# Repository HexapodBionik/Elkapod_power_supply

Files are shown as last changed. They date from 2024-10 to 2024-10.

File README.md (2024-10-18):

# Elkapod Power Supply
Elkapod Power Supply is a power supply for a hexapod walking robot built as part of the work in the Warsaw University of Technology Bionik science club. It provides power to 18 leg servos, electronics and peripherals.

---

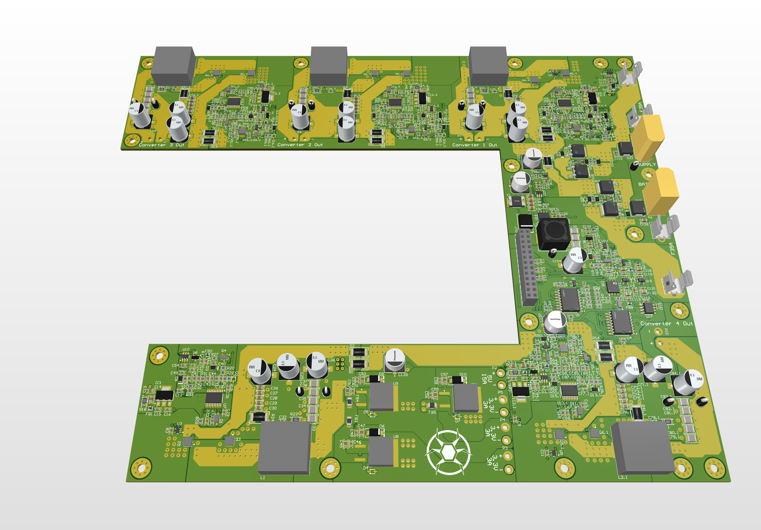
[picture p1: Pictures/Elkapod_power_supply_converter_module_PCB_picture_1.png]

The bottom PCB - Converter Module

---


The upper PCB -  Controller Module

## Design assumptions
The servos used in the project draw a maximum current of 3.5A according to the documentation. For this reason, the power supply should provide a current of around 60A. This power supply can be powered from an external mains power supply with a voltage of 11 to 18V, and from a lithium-ion battery with a similar voltage range. Therefore, it was decided to make 3 buck converters with a maximum current of 20A, which allow for tuning the output voltage in the range of 5.0-7.5V. Additionally, one 5V buck converter with a capacity of 15A was made to power the robot's electronics. The possibility of equipping the robot with an additional manipulator was also taken into account, by making an additional buck converter with a voltage regulated in the range of 5-9.5V and an output current of up to 20A. Additional requirements imposed on the power supply design were: measurement of the current of each servos, the ability to turn off the power supply of each servos separately, the use of logic level converters to control the servos using PWM from an external Elkapod Hardware Controller, additional controlled and uncontrolled 3.3V and 5V outputs, stand-by voltage outputs, voltage measurements, error status memory, communication with the battery pack using the SMBus protocol. All this is to be controlled from an external Elkapod Hardware Controller using the CAN bus.

The lower PCB contains 5 main converter sections, a stand-by converter and a power selector with reverse polarity protection implemented on MOSFET transistors.

The upper PCB contains circuits for measuring currents, controlling servos, a simple user interface based on buttons and LEDs and an STM32 microcontroller.

## Description of connectors

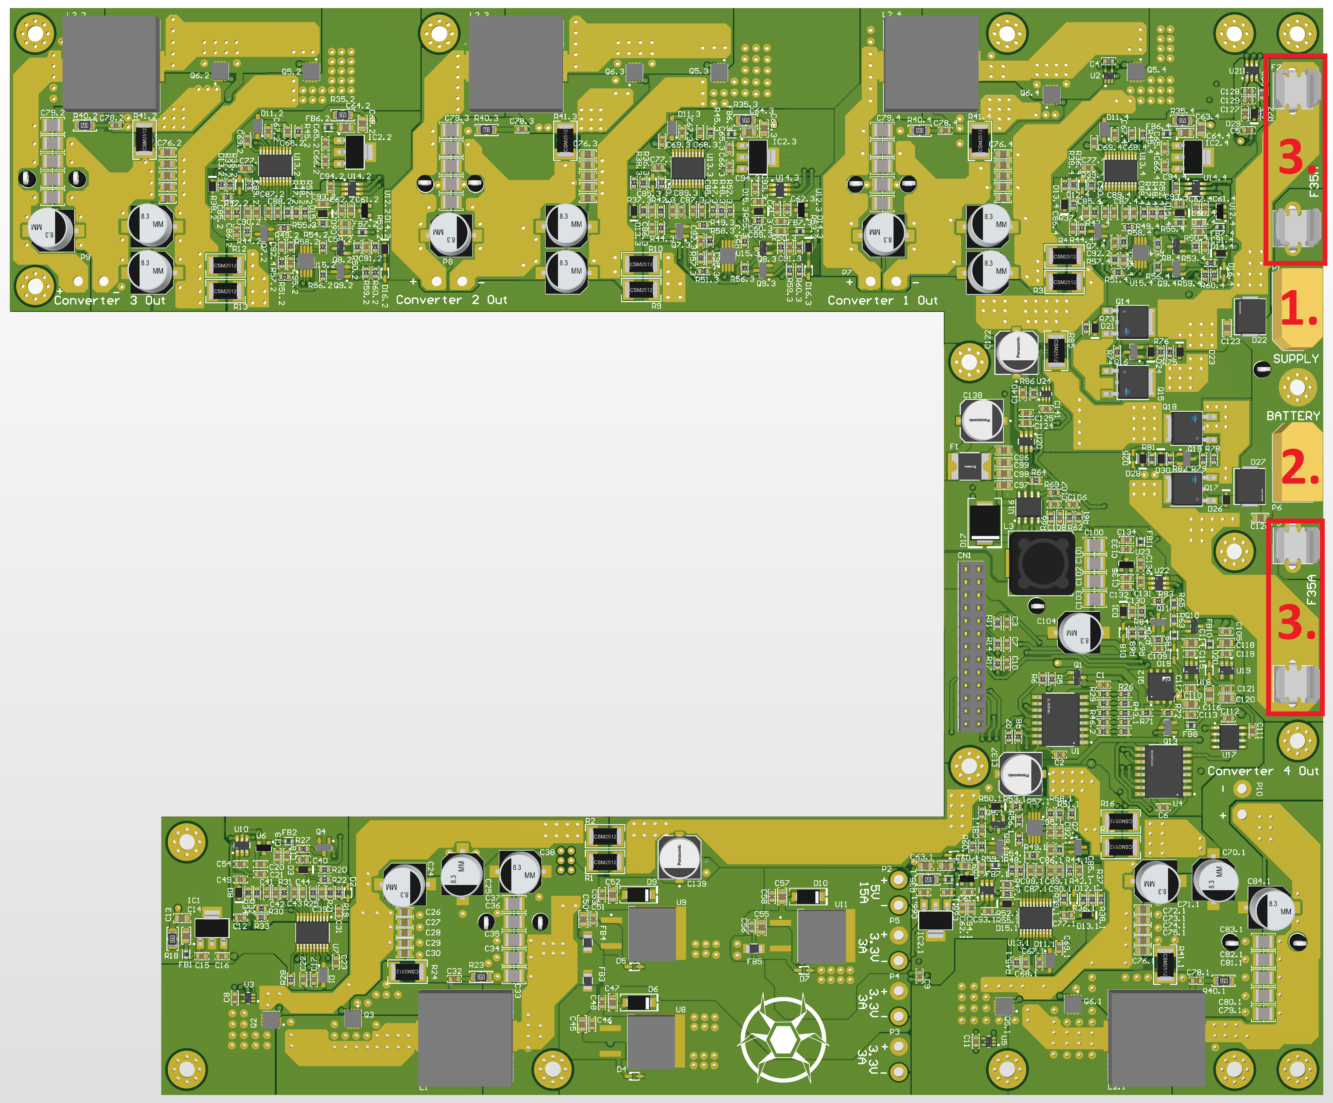
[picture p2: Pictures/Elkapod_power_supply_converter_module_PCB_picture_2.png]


The lower PCB:

1. External power supply XT60 connector (11-18V, min. 35A);
2. Li-ion battery pack XT60 connector (4s configuration);
3. 35A 6.3x32mm fast fuses connectors;

---

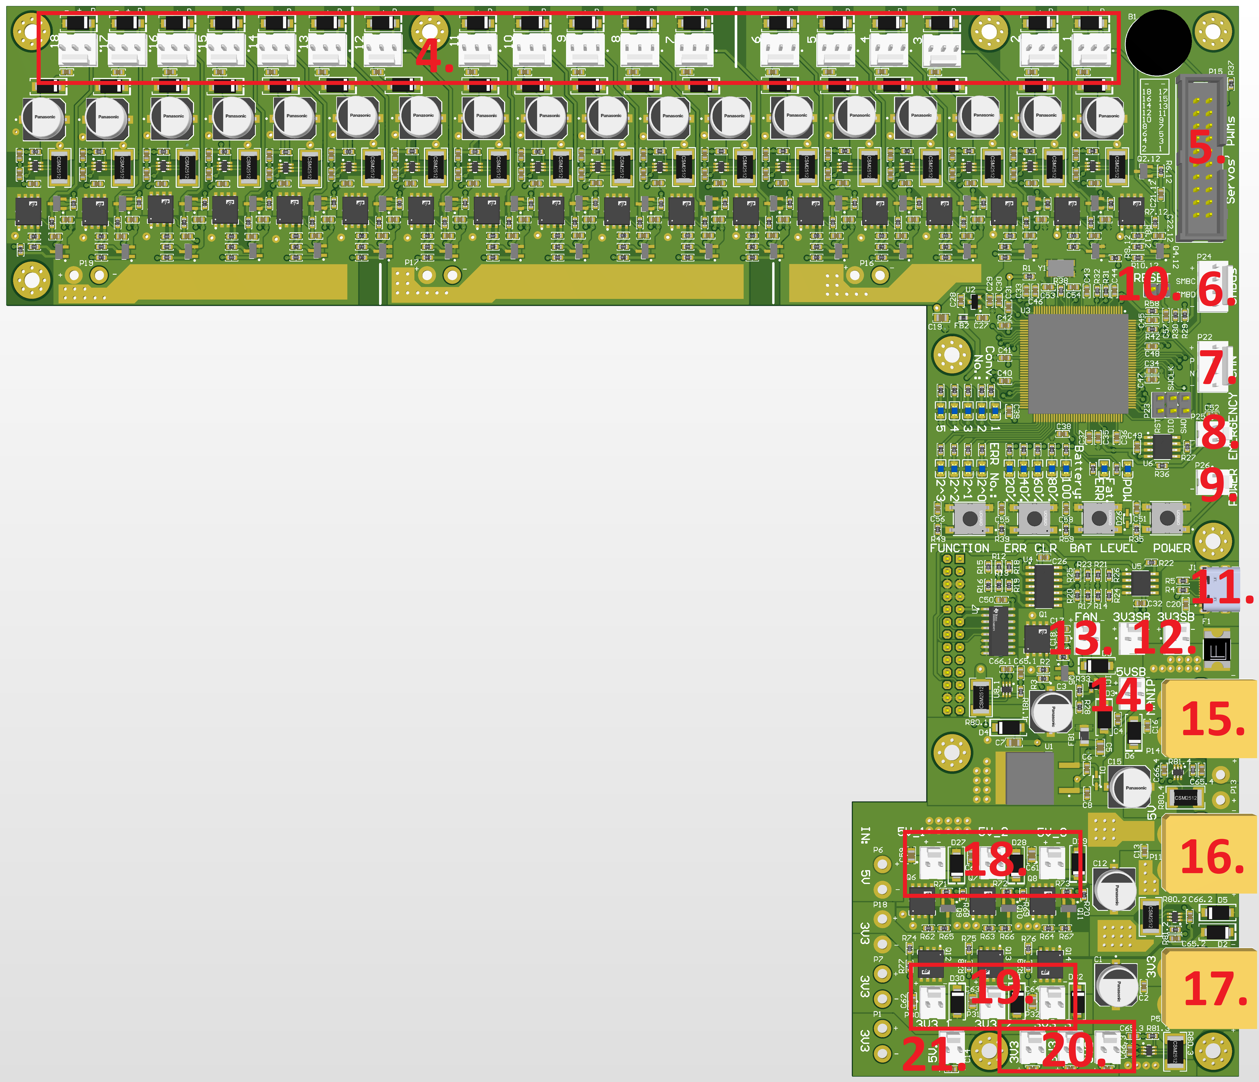
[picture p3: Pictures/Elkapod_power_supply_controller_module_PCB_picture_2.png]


The upper PCB:

4. 18 x servos connectors (5.0-7.5V; 3.5A);
5. IDC20 connector to control servos with PWM;
6. SMBus KK connector to control the battery li-ion pack;
7. CAN KK connector;
8. Emergency button KK connector (OFF-(ON) type);
9. Power button KK connector (OFF-(ON) type);
10. Reset goldpin jumper;
11. USB-C supply connector (5V; 5A);
12. 3.3V stand-by voltage KK connectors (sum of all 3.3V and 5V currents up to 2.5A);
13. Optional fan KK connector (5V; 100mA);
14. 5V stand-by voltage KK connector (sum of all 3.3V and 5V currents up to 2.5A);
15. Manipulator supply XT60 connector (5.0-9.5V; 20A);
16. 5V power out XT60 connector (up to 15A but sum of all 3.3V and 5V currents (except stand-by voltages) cannot exceed 15A);
17. 3.3V power out XT60 connector (3A);
18. 5V controllable (turn on and off via CAN bus) KK connectors (3 x 2.5A);
19. 3.3V controll controllable (turn on and off via CAN bus) KK connectors (3 x 2.5A but sum of all this currents cannot exceed 3A);
20. 3.3V KK connectors (3 x 2.5A but sum of all this currents cannot exceed 3A);
21. 5V KK connector;

## Safety information
The device is built exclusively from MOSFET transistors and integrated circuits in MOS technology, which makes it very sensitive to ESD (electrostatic discharge). All connectors are protected against ESD using Transil diodes, but this does not protect against damaging the board by touching it in other places. Therefore, it is forbidden to touch the power supply without appropriate anti-ESD protection.

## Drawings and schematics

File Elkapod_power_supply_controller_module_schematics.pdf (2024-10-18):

# DC Outputs

# Currents Measurement

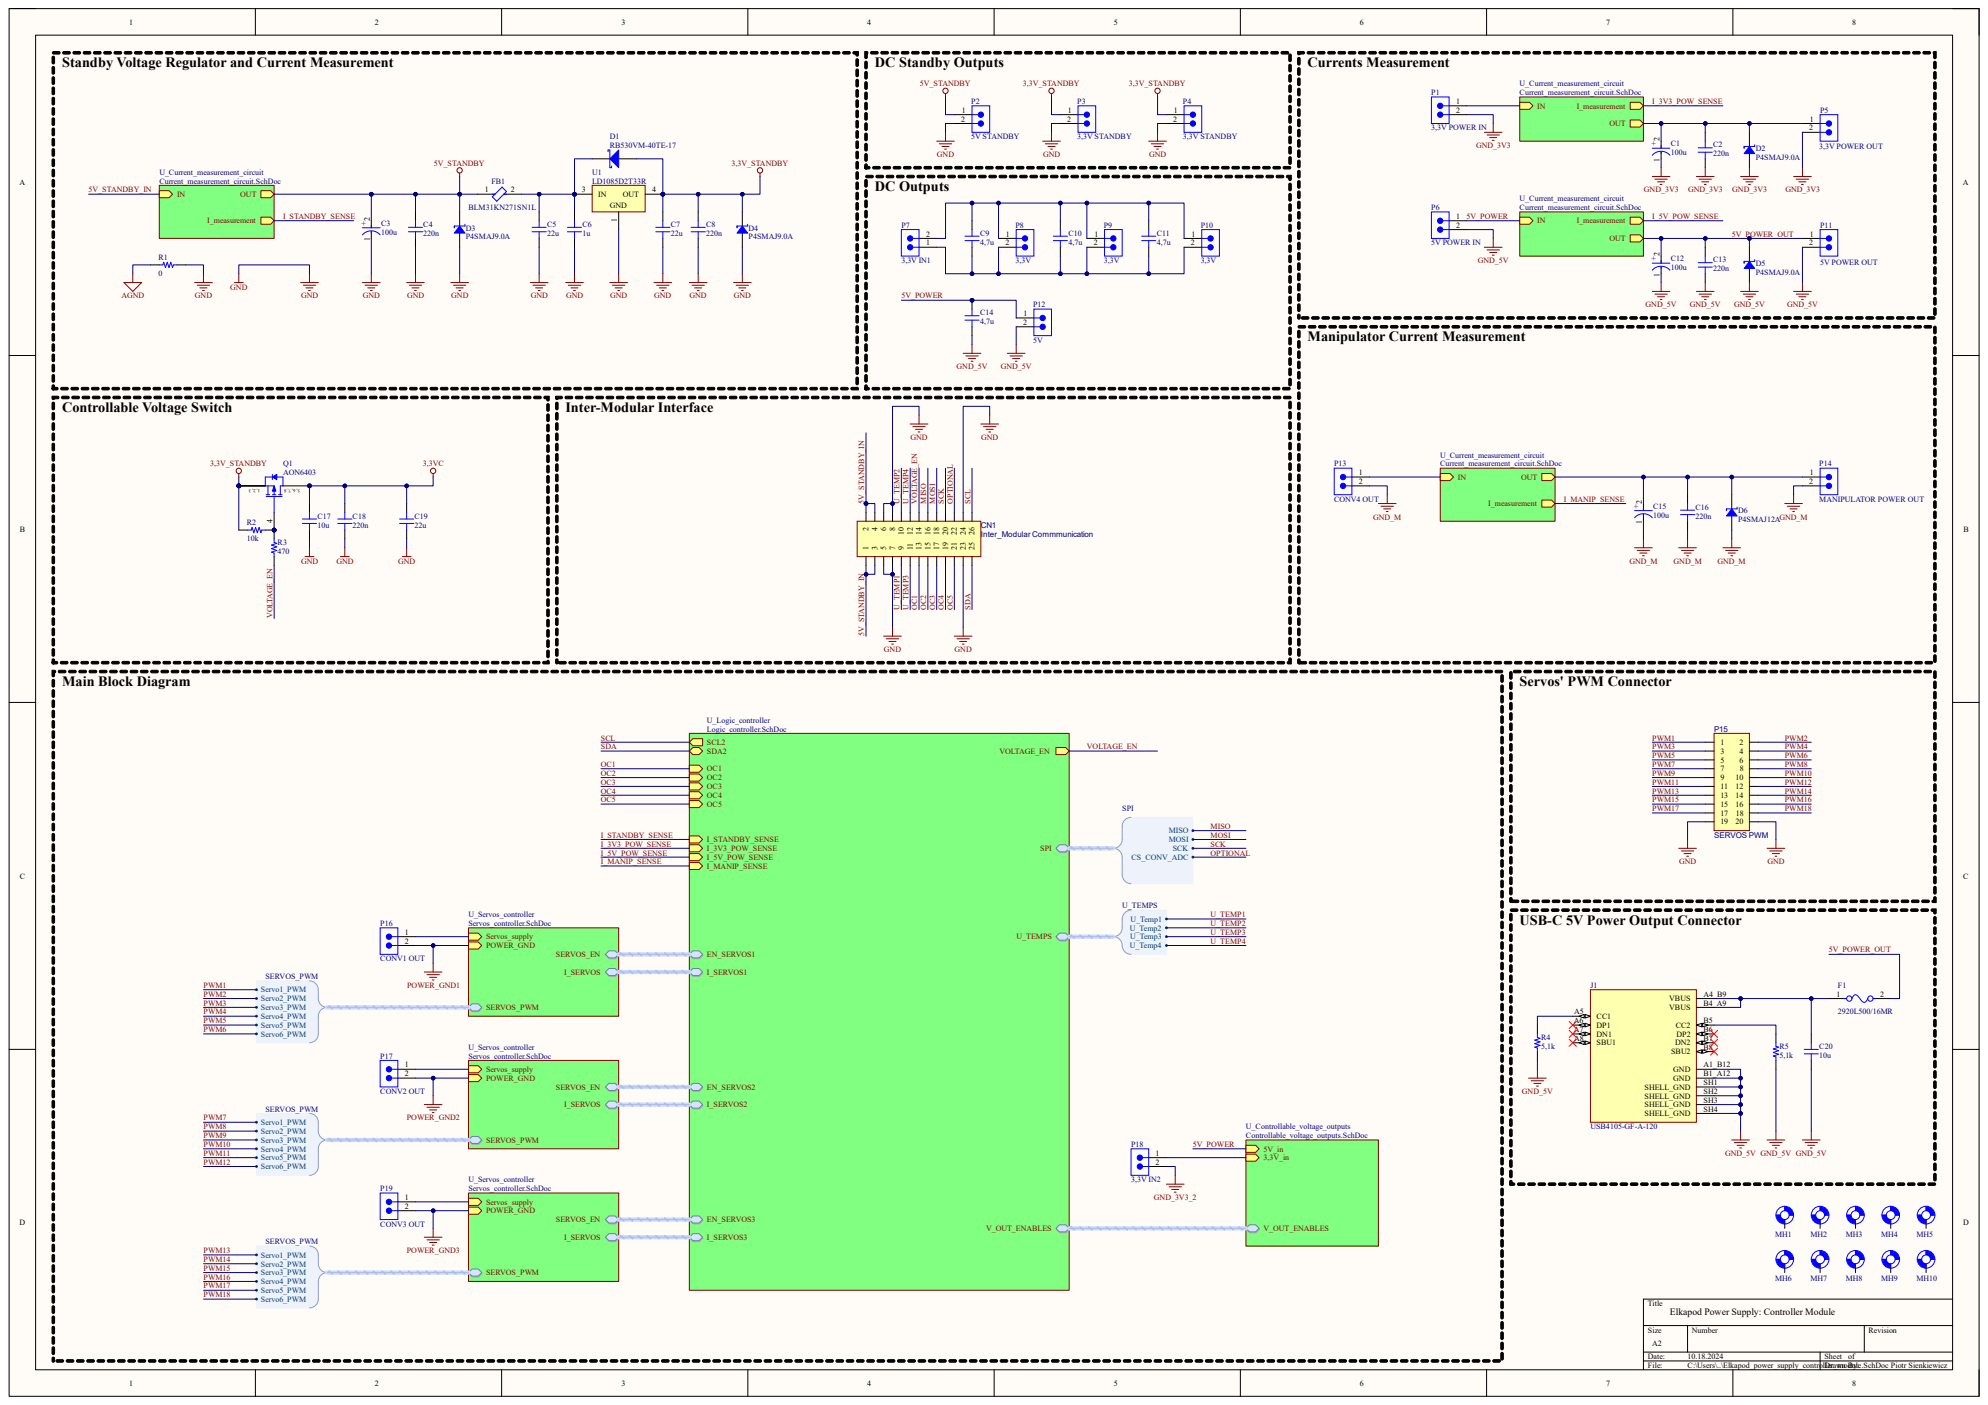
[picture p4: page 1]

Standby Voltage Regulator and Current Measurement

USB-C 5V Power Output Connector

Title
Elkapod Power Supply: Controller Module

A A

# Servos_supply

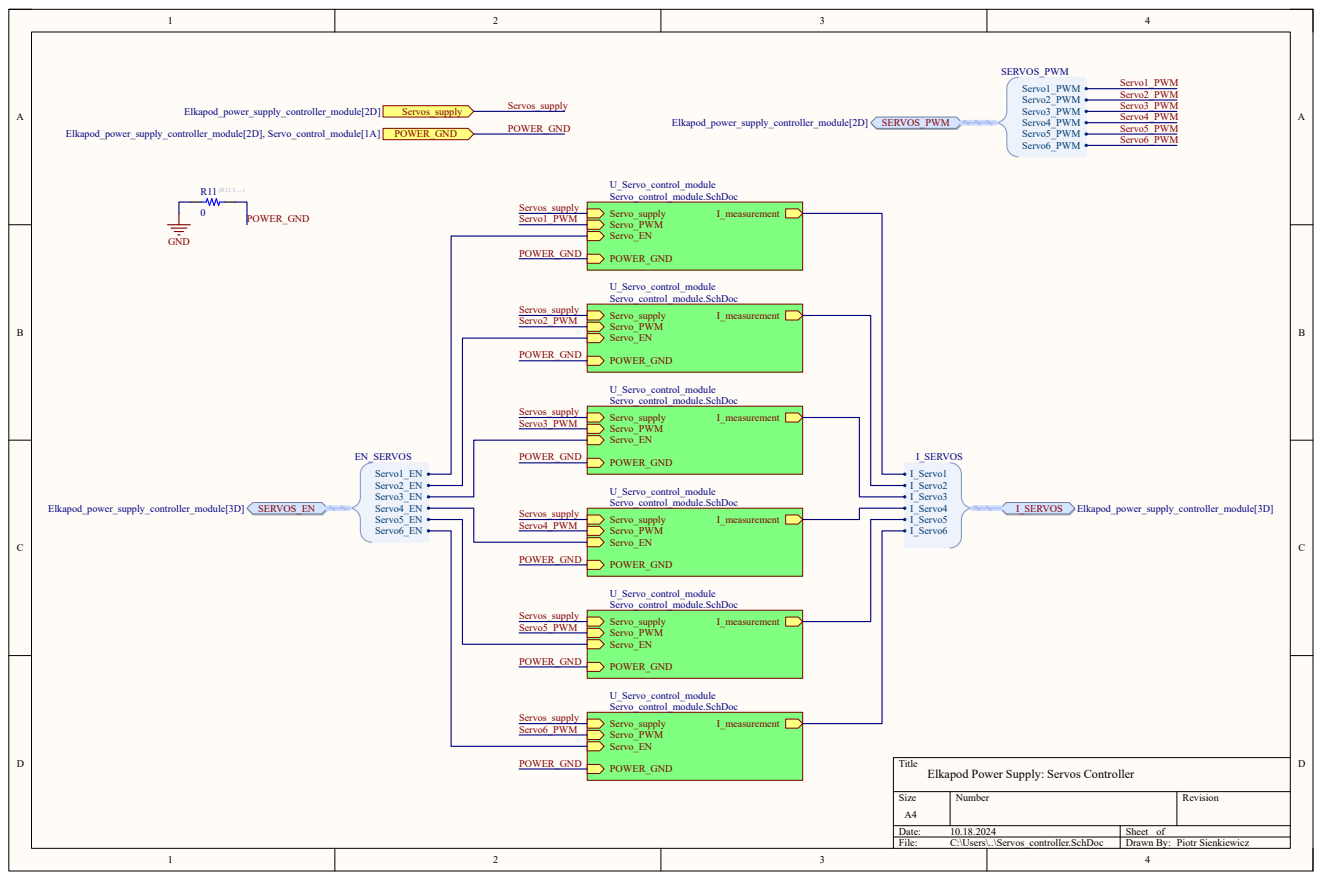
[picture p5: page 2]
Size; Number; Revision; File:; C:\Users\..\Servos_controller.SchDoc; Drawn By:; Servos_supply; Servo1_PWM; Servo2_PWM; Servo3_PWM; Servo4_PWM; Servo5_PWM; Servo6_PWM; Servo_supply Servo_PWM; I_measurement; Servo_EN; POWER_GND; U_Servo_control_module Servo_control_module.SchDoc; Elkapod_power_supply_controller_module[2D]; I_Servo1 I_Servo2 I_Servo3 I_Servo4 I_Servo5 I_Servo6; I_SERVOS; Elkapod_power_supply_controller_module[3D]; Servo1_EN Servo2_EN Servo3_EN Servo4_EN Servo5_EN Servo6_EN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

Title
Elkapod Power Supply: Servos Controller

A A

Servo_supply | Servo_supply

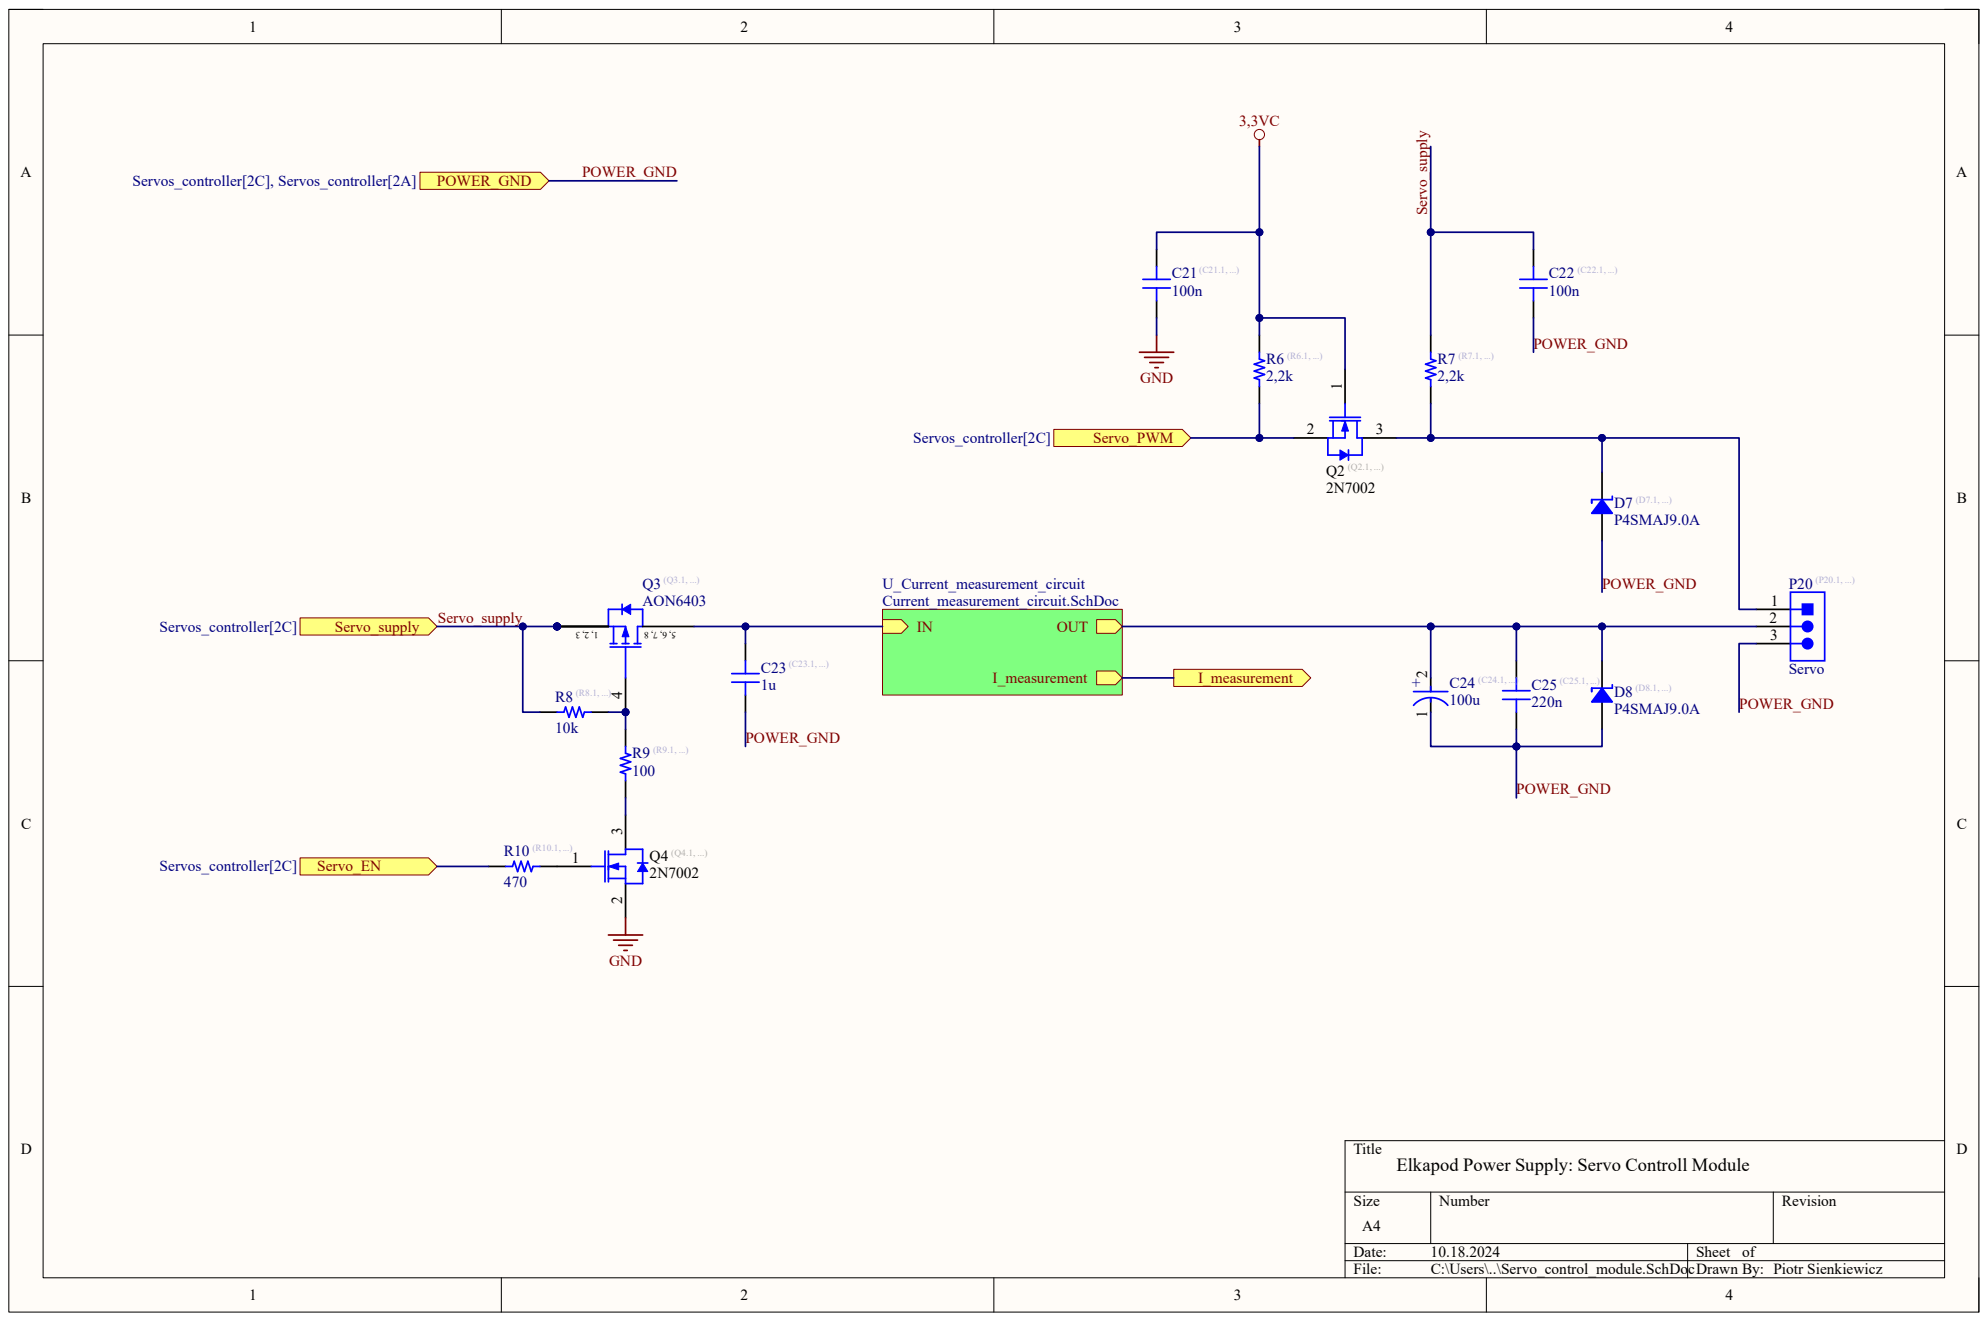
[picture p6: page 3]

Title
Elkapod Power Supply: Servo Controll Module

# MCU Power Supply

# Overcurrent Signals Comparators

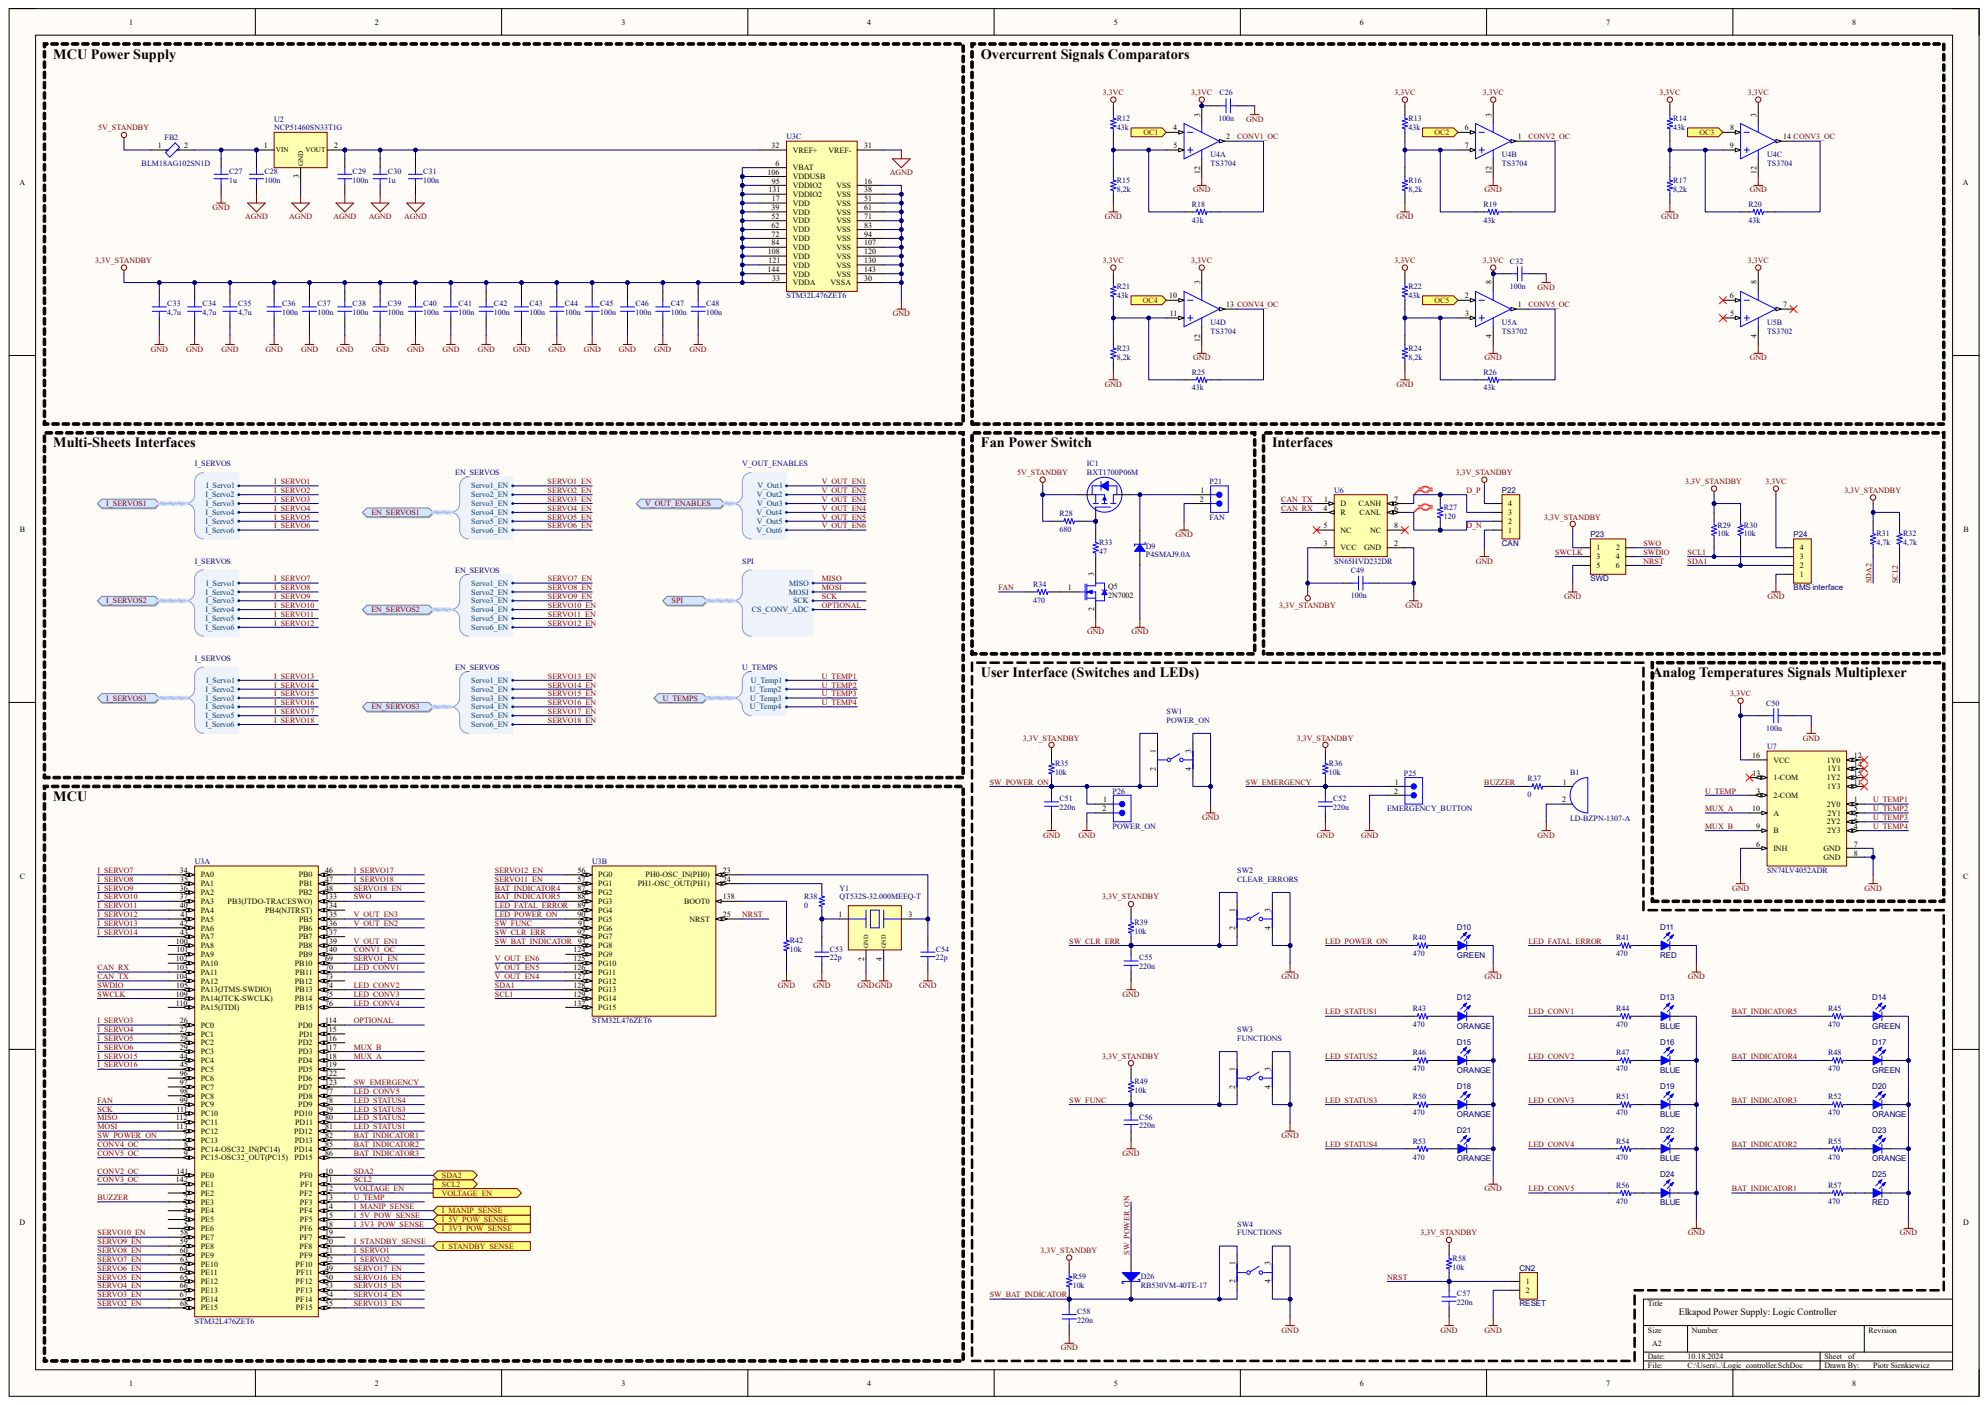
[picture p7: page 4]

User Interface (Switches and LEDs)

Analog Temperatures Signals Multiplexer

Title
Elkapod Power Supply: Logic Controller

A A

# 5V Controllable Outputs

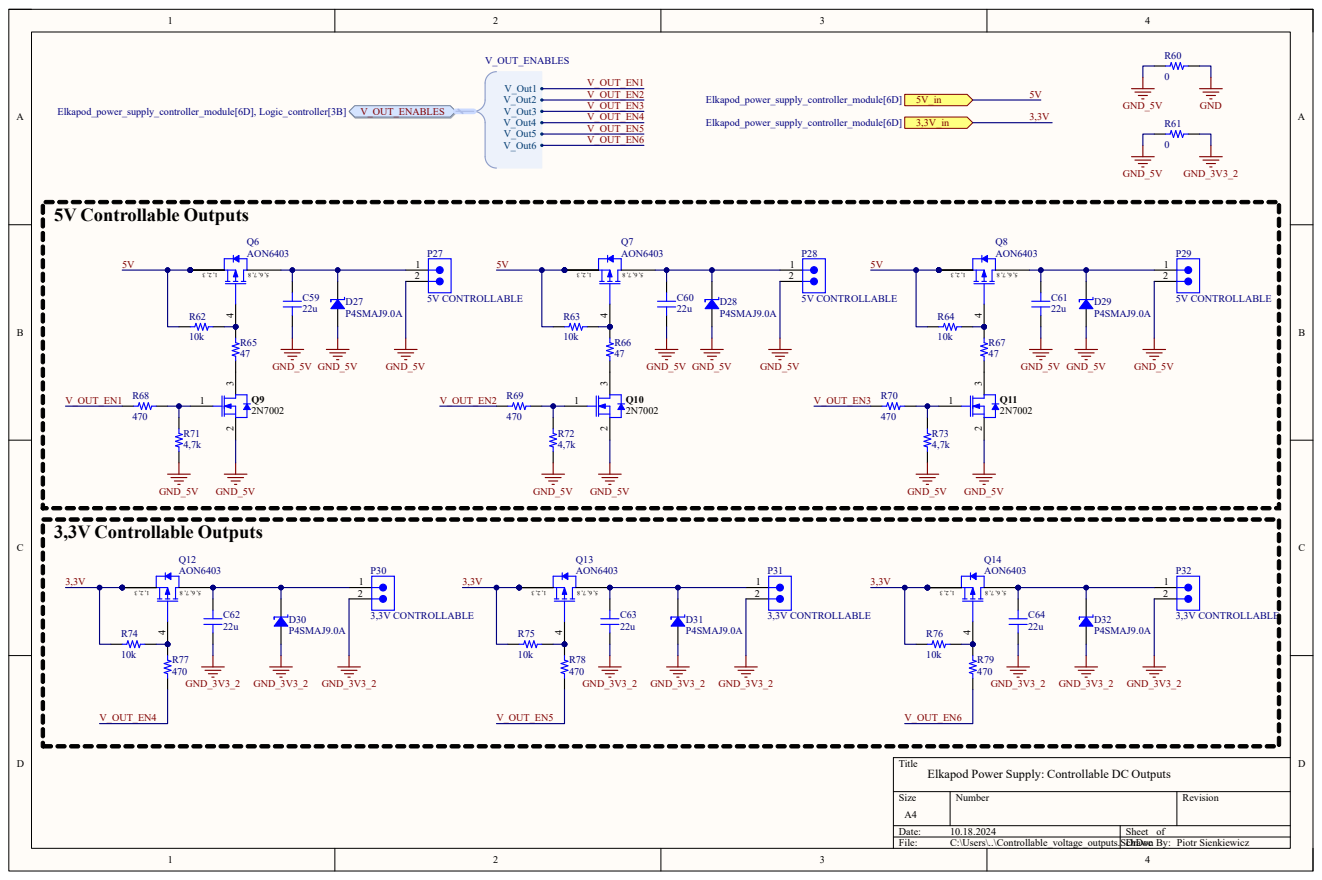
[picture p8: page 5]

Title
Elkapod Power Supply: Controllable DC Outputs

A A

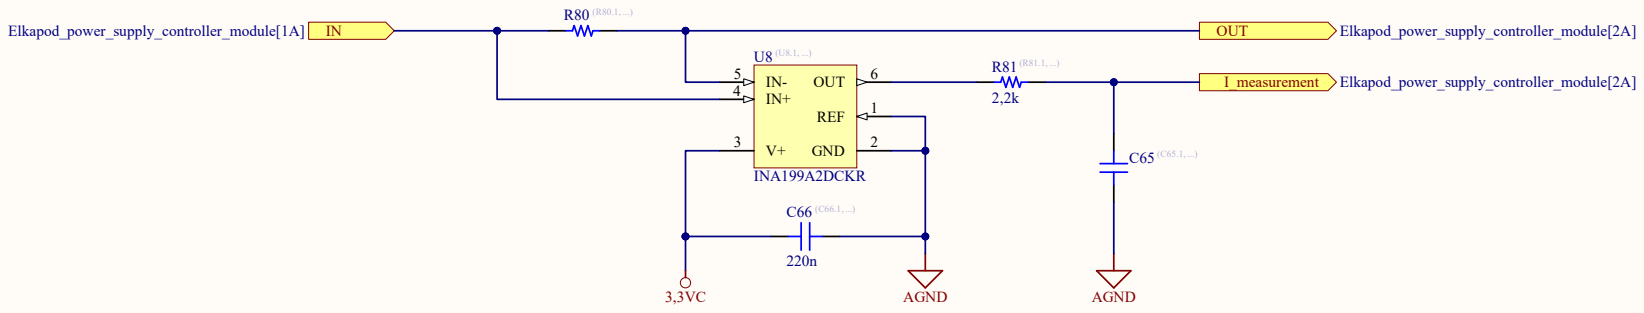
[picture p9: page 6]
Size; Number; Revision; File:; C:\Users\..\Current_measurement_circuit.SchDoc Drawn By:; GND; OUT; REF; INA199A2DCKR; AGND; I_measurement; Elkapod_power_supply_controller_module[2A]; Elkapod_power_supply_controller_module[1A]

Title
Elkapod Power Supply: Current Measurement

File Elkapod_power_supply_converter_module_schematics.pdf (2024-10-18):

# GND VOLTAGE_EN MISO MOSI CLK SCL

# Inter-Modular Communication Socket

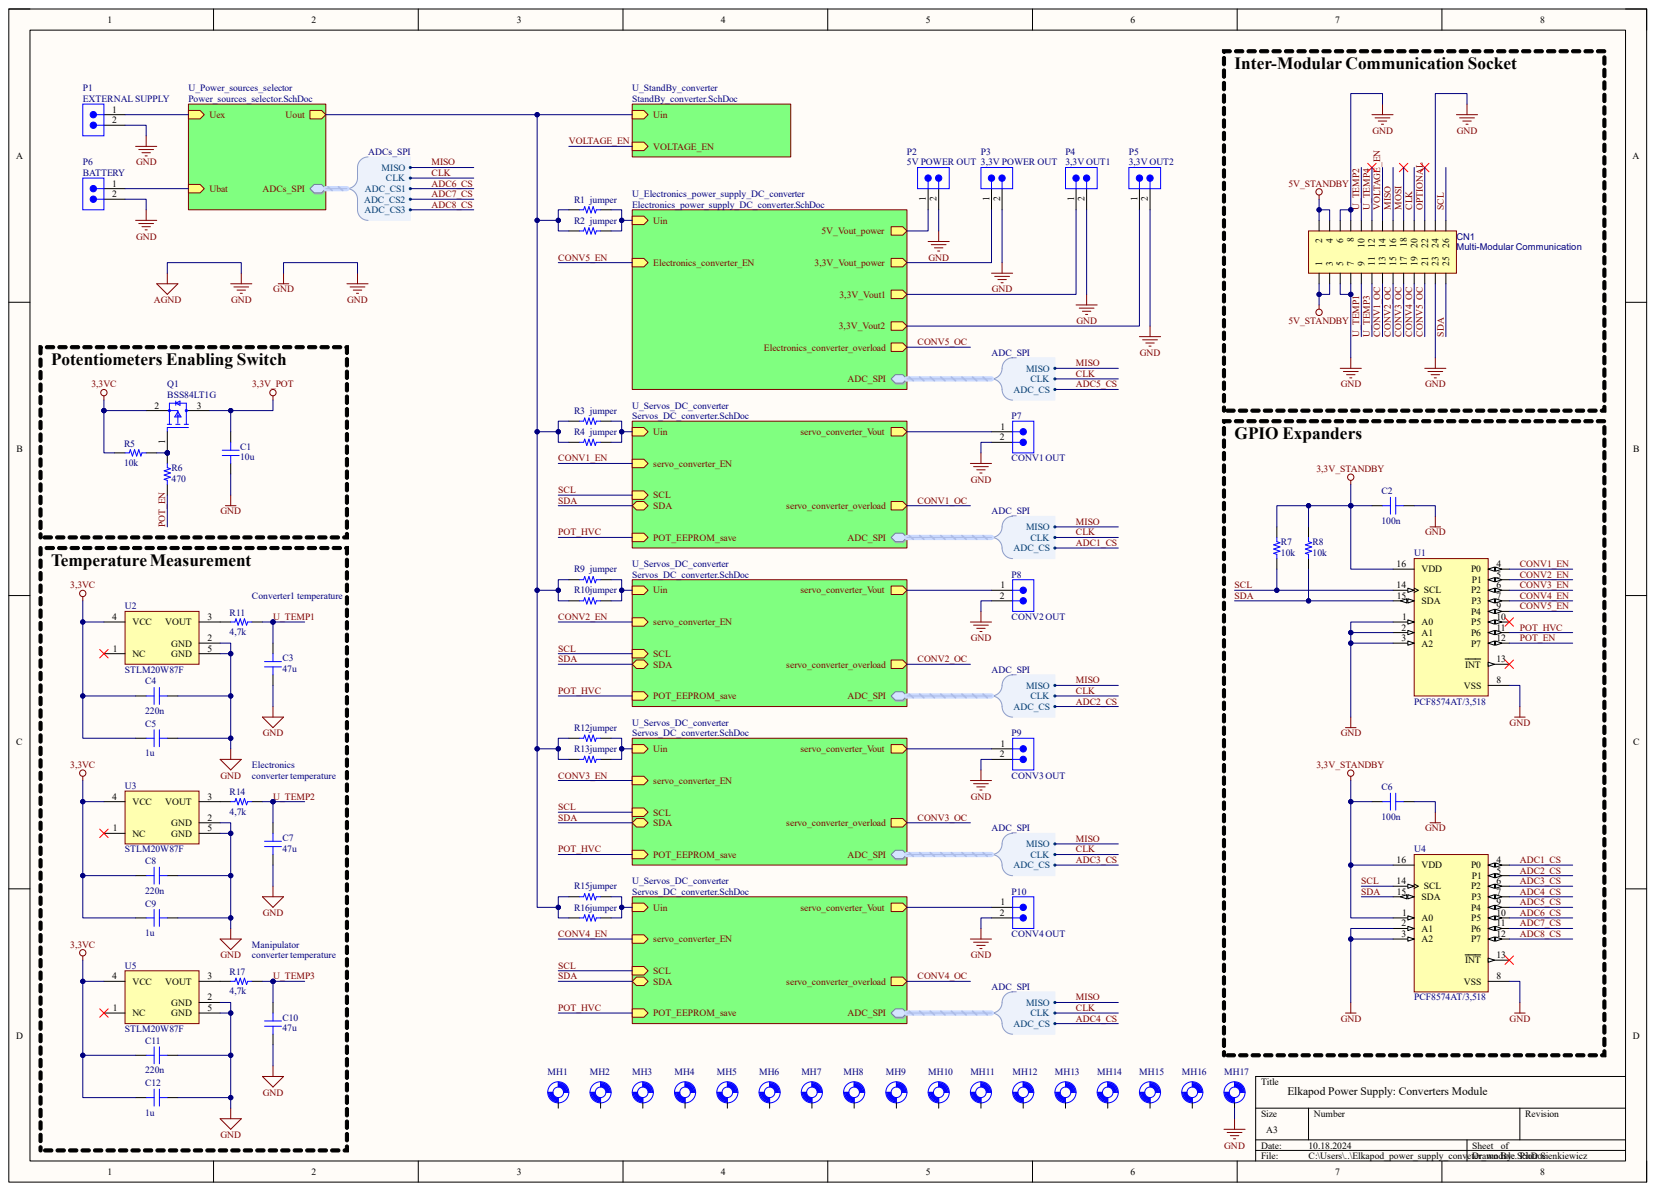
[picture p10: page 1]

Title
Elkapod Power Supply: Converters Module

# 3,3V Controllable ADC Reference Voltage

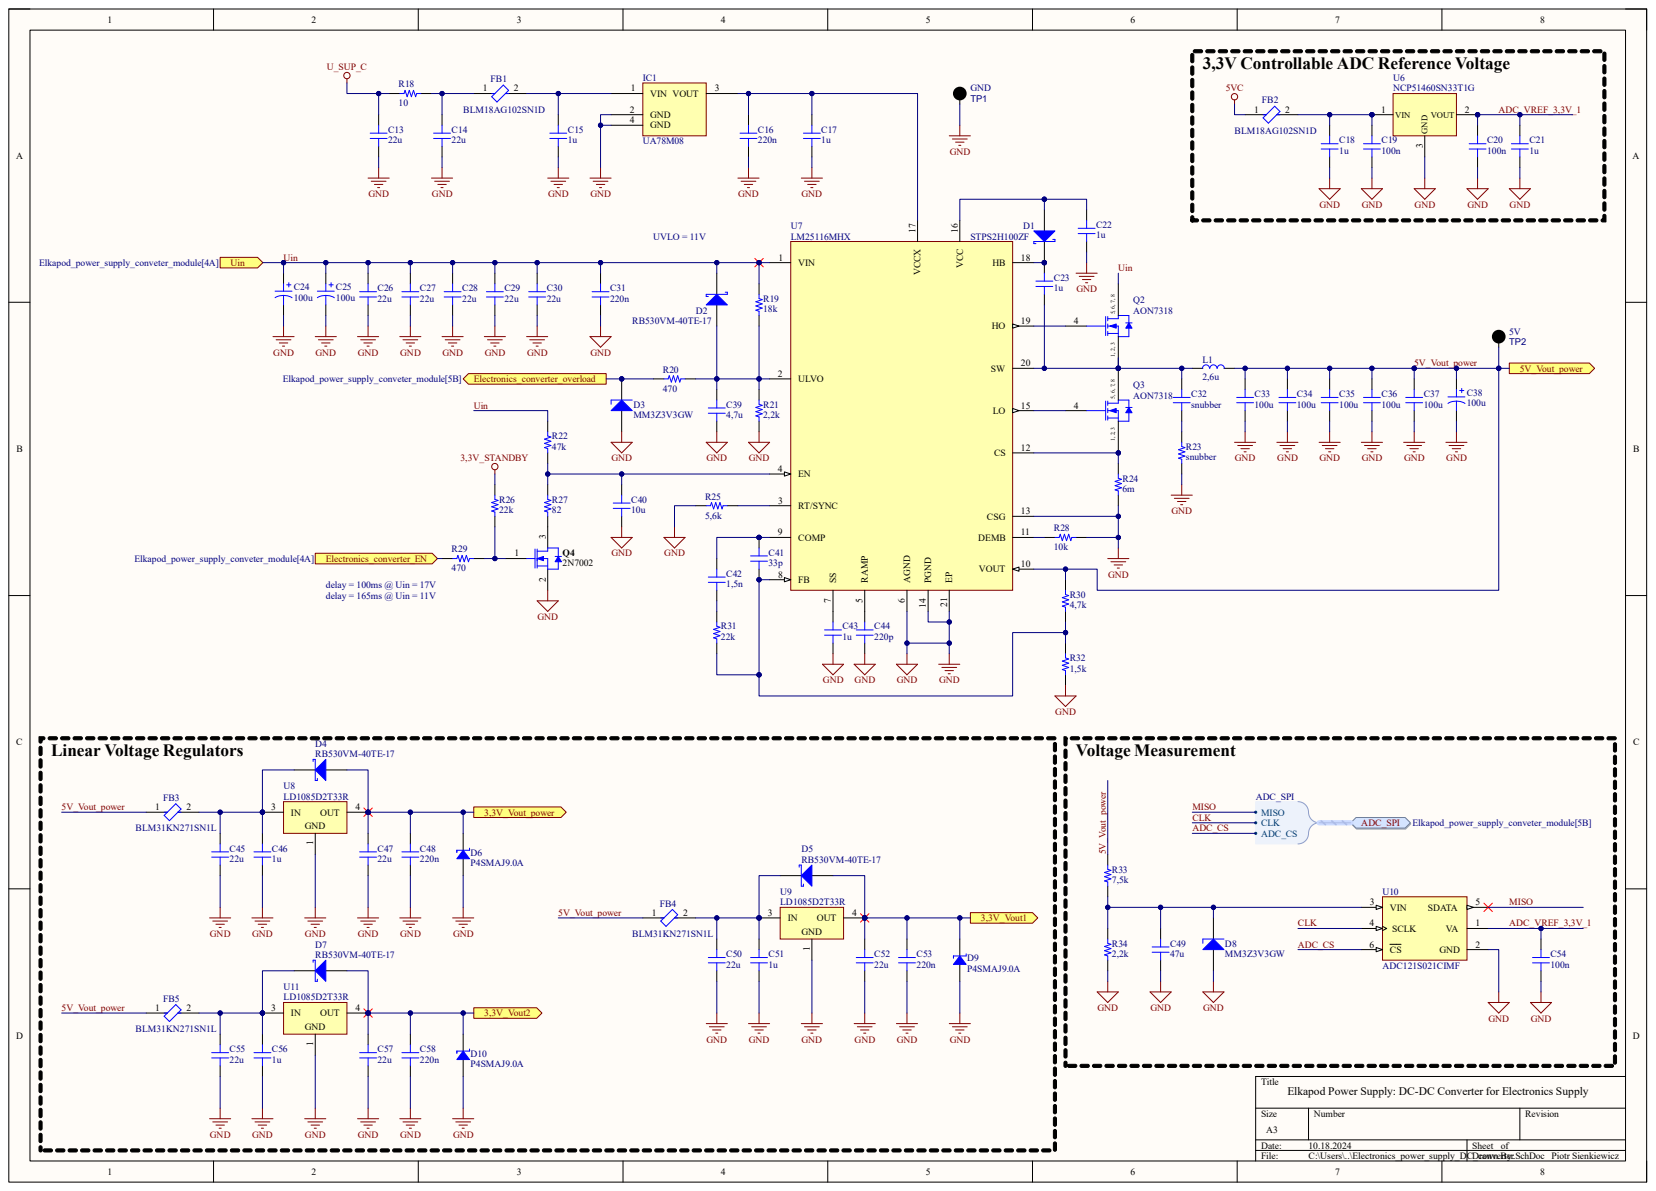
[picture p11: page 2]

Title
Elkapod Power Supply: DC-DC Converter for Electronics Supply

# 3,3V Controllable ADC Reference Voltage

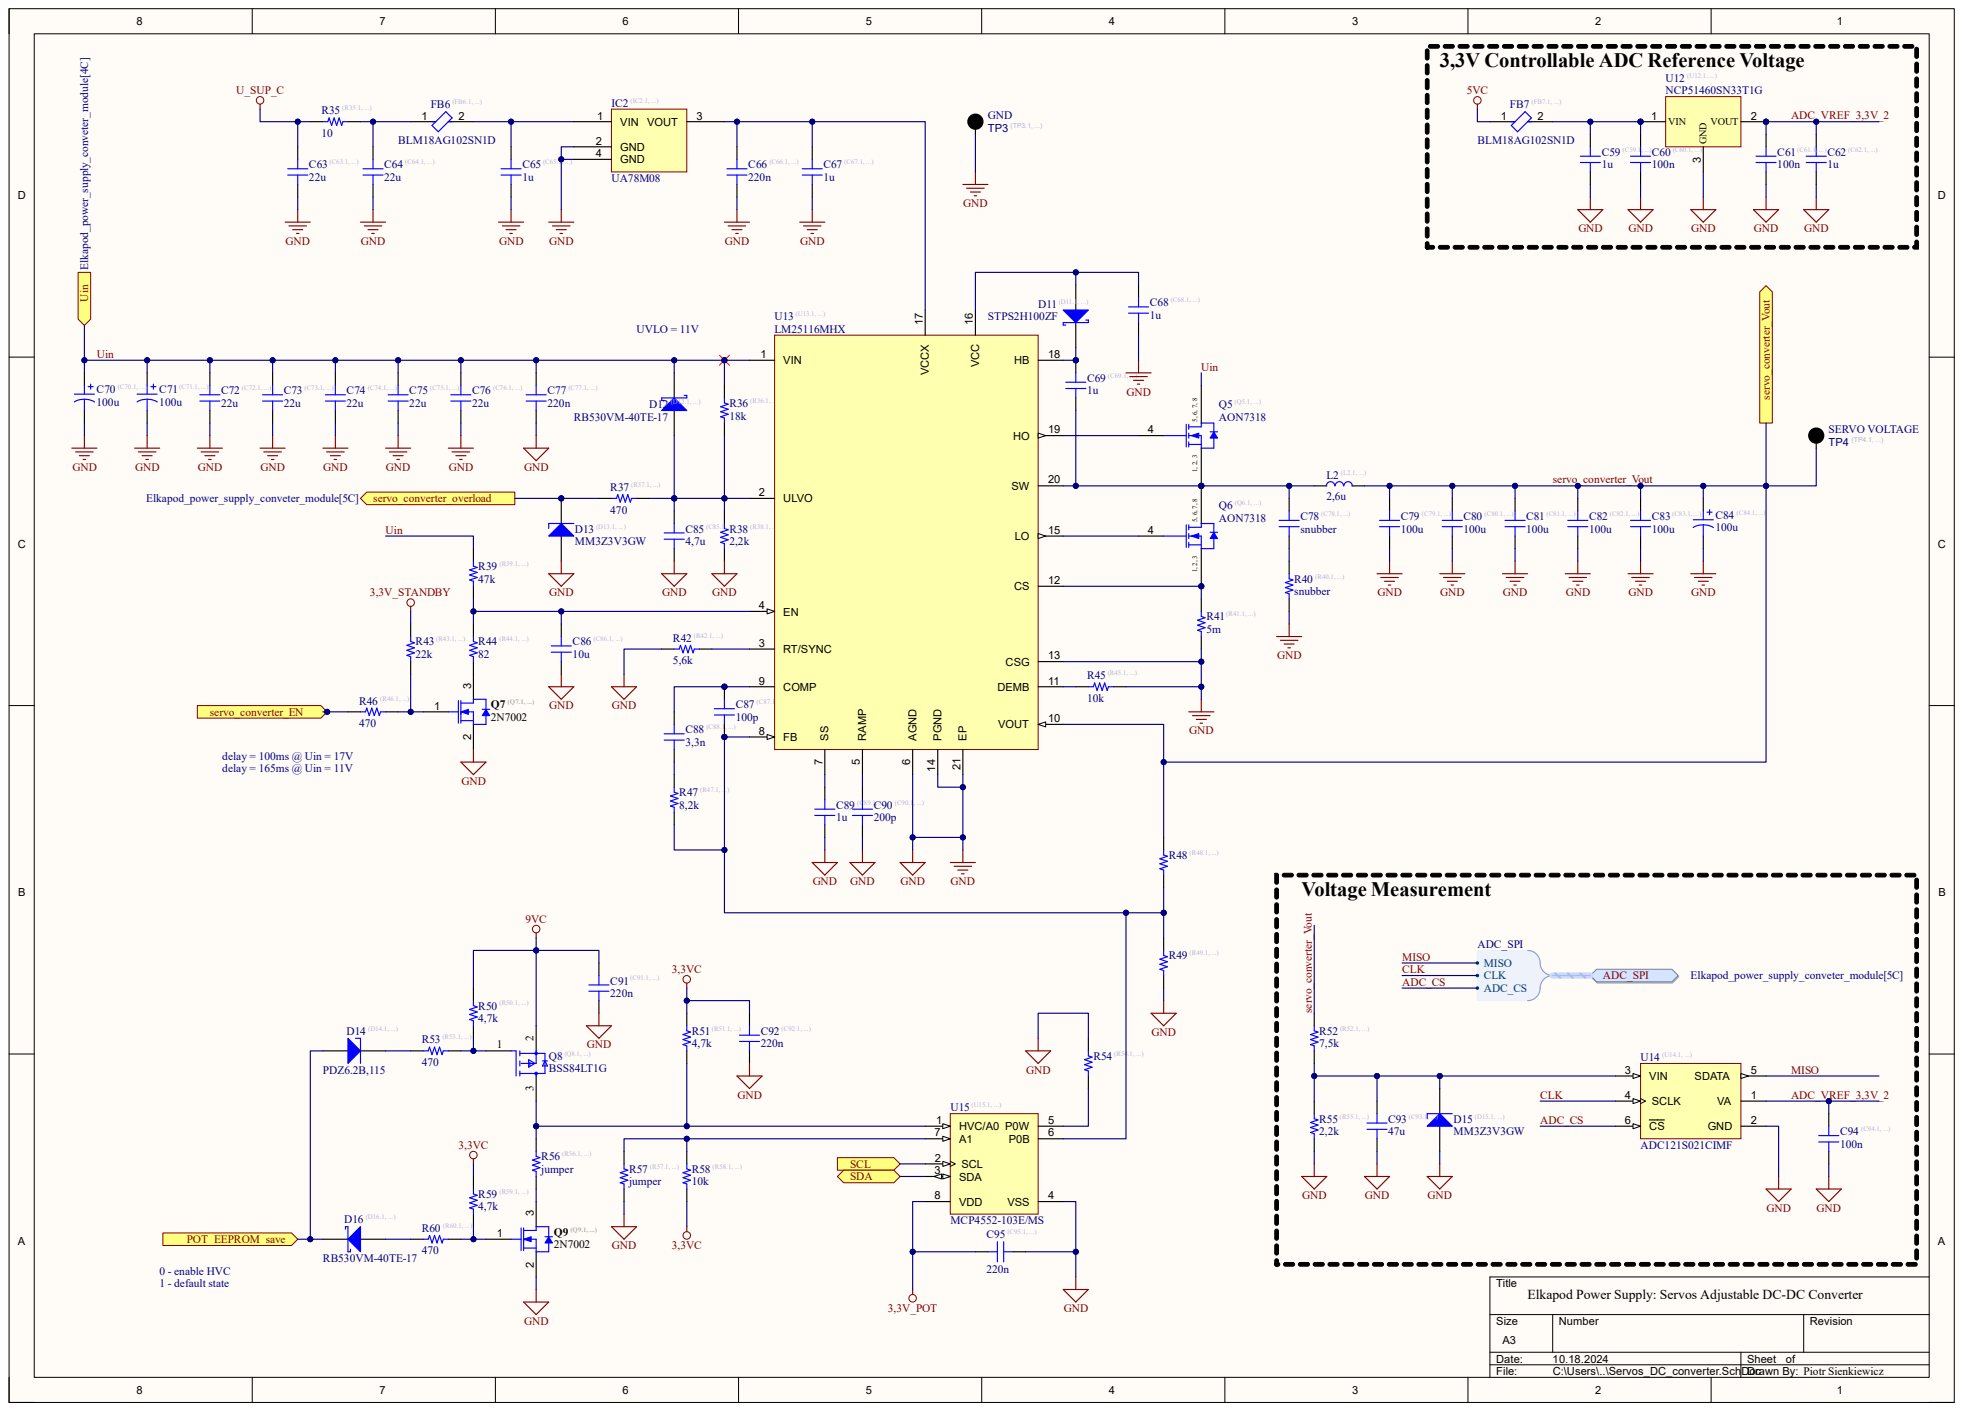
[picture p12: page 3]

Title
Elkapod Power Supply: Servos Adjustable DC-DC Converter

A A

22u

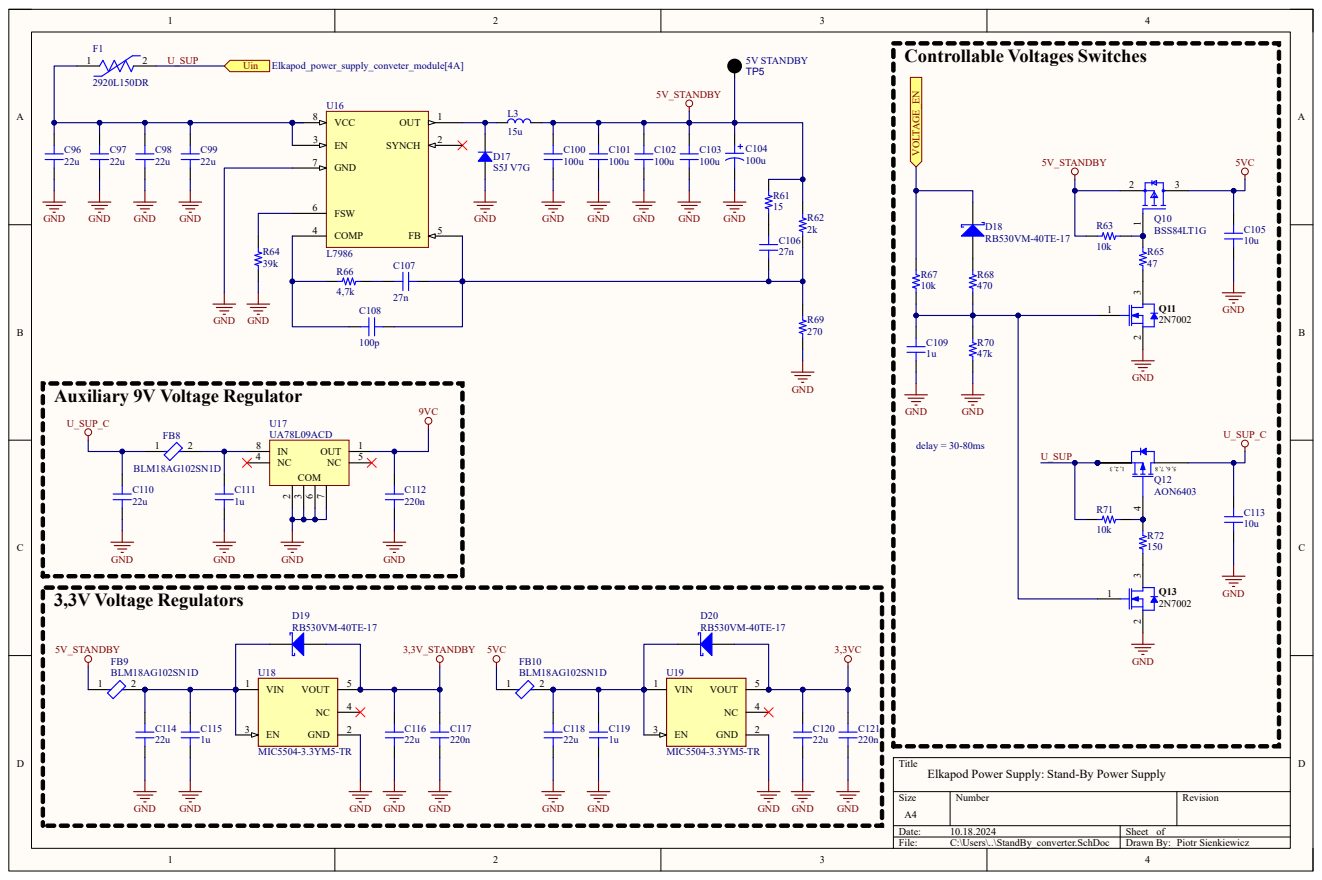
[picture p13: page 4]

Title
Elkapod Power Supply: Stand-By Power Supply

A A

4 3

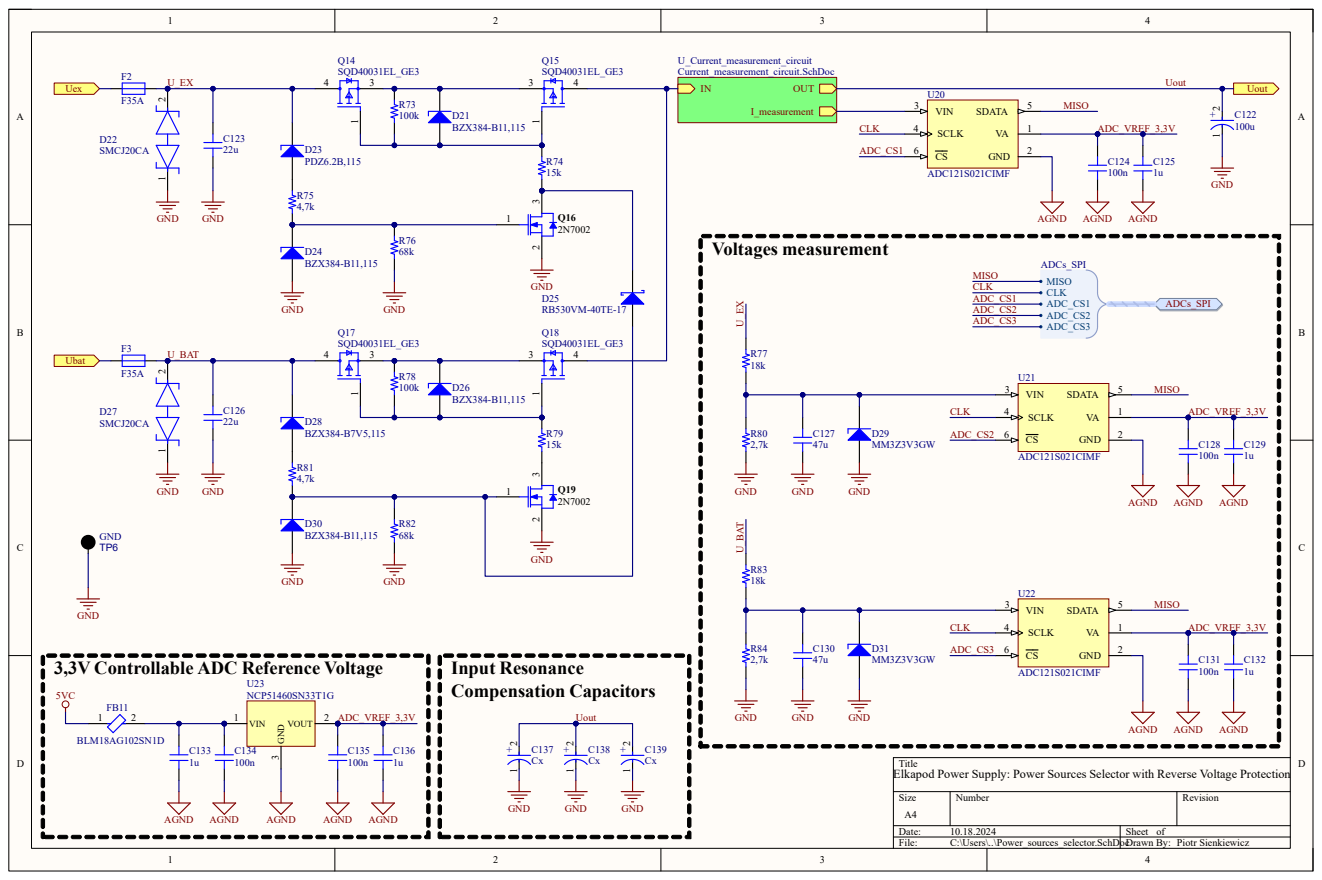
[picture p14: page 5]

3,3V Controllable ADC Reference Voltage

Title
Elkapod Power Supply: Power Sources Selector with Reverse Voltage Protection

A A

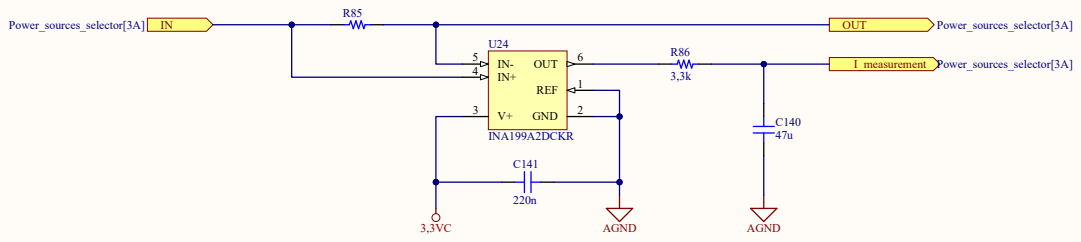
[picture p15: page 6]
Size; Number; Revision; File:; C:\Users\..\Current_measurement_circuit.SchDoc Drawn By:; GND; OUT; REF; INA199A2DCKR; AGND; I_measurement Power_sources_selector[3A]; Power_sources_selector[3A] IN; Power_sources_selector[3A]

Title
Elkapod Power Supply: Current Measurement

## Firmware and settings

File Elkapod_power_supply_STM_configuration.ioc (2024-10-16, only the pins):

Mcu.UserName=STM32L476ZETx
PA0.GPIO_Label=I_SERVO7
PA0.Signal=ADCx_IN5
PA1.GPIO_Label=I_SERVO8
PA1.Signal=ADCx_IN6
PA11.Signal=CAN1_RX
PA12.Signal=CAN1_TX
PA2.GPIO_Label=I_SERVO9
PA2.Signal=ADCx_IN7
PA3.GPIO_Label=I_SERVO10
PA3.Signal=ADCx_IN8
PA4.GPIO_Label=I_SERVO11
PA4.Signal=ADCx_IN9
PA5.GPIO_Label=I_SERVO12
PA5.Signal=ADCx_IN10
PA6.GPIO_Label=I_SERVO13
PA6.Signal=ADCx_IN11
PA7.GPIO_Label=I_SERVO14
PA7.Signal=ADCx_IN12
PB0.GPIO_Label=I_SERVO17
PB0.Signal=ADCx_IN15
PB1.GPIO_Label=I_SERVO18
PB1.Signal=ADCx_IN16
PB10.GPIO_Label=SERVO1_EN
PB10.Signal=GPIO_Output
PB11.GPIO_Label=LED_CONV1
PB11.Signal=GPIO_Output
PB13.GPIO_Label=LED_CONV2
PB13.Signal=GPIO_Output
PB14.GPIO_Label=LED_CONV3
PB14.Signal=GPIO_Output
PB15.GPIO_Label=LED_CONV4
PB15.Signal=GPIO_Output
PB2.GPIO_Label=SERVO18_EN
PB2.Signal=GPIO_Output
PB5.GPIO_Label=V_OUT_EN3
PB5.Signal=GPIO_Output
PB6.GPIO_Label=V_OUT_EN2
PB6.Signal=GPIO_Output
PB8.GPIO_Label=V_OUT_EN1
PB8.Signal=GPIO_Output
PB9.GPIO_Label=CONV1_OC
PB9.Signal=GPXTI9
PC0.GPIO_Label=I_SERVO3
PC0.Signal=ADCx_IN1
PC1.GPIO_Label=I_SERVO4
PC1.Signal=ADCx_IN2
PC10.Signal=SPI3_SCK
PC11.Signal=SPI3_MISO
PC12.Signal=SPI3_MOSI
PC13.GPIO_Label=SW_POWER_ON
PC13.Signal=SYS_WKUP2
PC2.GPIO_Label=I_SERVO5
PC2.Signal=ADCx_IN3
PC3.GPIO_Label=I_SERVO6
PC3.Signal=ADCx_IN4
PC4.GPIO_Label=I_SERVO15
PC4.Signal=ADCx_IN13
PC5.GPIO_Label=I_SERVO16
PC5.Signal=ADCx_IN14
PC9.GPIO_Label=FAN
PC9.Signal=S_TIM8_CH4
PD0.GPIO_Label=OPTIONAL
PD0.Signal=GPIO_Output
PD10.GPIO_Label=LED_STATUS3
PD10.Signal=GPIO_Output
PD11.GPIO_Label=LED_STATUS2
PD11.Signal=GPIO_Output
PD12.GPIO_Label=LED_STATUS1
PD12.Signal=GPIO_Output
PD13.GPIO_Label=BAT_INDICATOR1
PD13.Signal=GPIO_Output
PD14.GPIO_Label=BAT_INDICATOR2
PD14.Signal=GPIO_Output
PD15.GPIO_Label=BAT_INDICATOR3
PD15.Signal=GPIO_Output
PD3.GPIO_Label=MUX_B
PD3.Signal=GPIO_Output
PD4.GPIO_Label=MUX_A
PD4.Signal=GPIO_Output
PD7.GPIO_Label=SW_EMERGENCY
PD7.Signal=GPXTI7
PD8.GPIO_Label=LED_CONV5
PD8.Signal=GPIO_Output
PD9.GPIO_Label=LED_STATUS4
PD9.Signal=GPIO_Output
PE0.GPIO_Label=CONV2_OC
PE0.Signal=GPXTI0
PE1.GPIO_Label=CONV3_OC
PE1.Signal=GPXTI1
PE10.GPIO_Label=SERVO7_EN
PE10.Signal=GPIO_Output
PE11.GPIO_Label=SERVO6_EN
PE11.Signal=GPIO_Output
PE12.GPIO_Label=SERVO5_EN
PE12.Signal=GPIO_Output
PE13.GPIO_Label=SERVO4_EN
PE13.Signal=GPIO_Output
PE14.GPIO_Label=SERVO3_EN
PE14.Signal=GPIO_Output
PE15.GPIO_Label=SERVO2_EN
PE15.Signal=GPIO_Output
PE3.GPIO_Label=BUZZER
PE3.Signal=S_TIM3_CH1
PE7.GPIO_Label=SERVO10_EN
PE7.Signal=GPIO_Output
PE8.GPIO_Label=SERVO9_EN
PE8.Signal=GPIO_Output
PE9.GPIO_Label=SERVO8_EN
PE9.Signal=GPIO_Output
PF0.Signal=I2C2_SDA
PF1.Signal=I2C2_SCL
PF10.GPIO_Label=I_SERVO2
PF10.Signal=ADC3_IN13
PF11.GPIO_Label=SERVO17_EN
PF11.Signal=GPIO_Output
PF12.GPIO_Label=SERVO16_EN
PF12.Signal=GPIO_Output
PF13.GPIO_Label=SERVO15_EN
PF13.Signal=GPIO_Output
PF14.GPIO_Label=SERVO14_EN
PF14.Signal=GPIO_Output
PF15.GPIO_Label=SERVO13_EN
PF15.Signal=GPIO_Output
PF2.GPIO_Label=VOLTAGE_EN
PF2.Signal=GPIO_Output
PF3.GPIO_Label=U_TEMP
PF3.Signal=ADC3_IN6
PF4.GPIO_Label=I_MANIP_SENSE
PF4.Signal=ADC3_IN7
PF5.GPIO_Label=I_5V_POW_SENSE
PF5.Signal=ADC3_IN8
PF6.GPIO_Label=I_3V3_POW_SENSE
PF6.Signal=ADC3_IN9
PF8.GPIO_Label=I_STANDBY_SENSE
PF8.Signal=ADC3_IN11
PF9.GPIO_Label=I_SERVO1
PF9.Signal=ADC3_IN12
PG0.GPIO_Label=SERVO12_EN
PG0.Signal=GPIO_Output
PG1.GPIO_Label=SERVO11_EN
PG1.Signal=GPIO_Output
PG10.GPIO_Label=V_OUT_EN6
PG10.Signal=GPIO_Output
PG11.GPIO_Label=V_OUT_EN5
PG11.Signal=GPIO_Output
PG12.GPIO_Label=V_OUT_EN4
PG12.Signal=GPIO_Output
PG13.Signal=I2C1_SDA
PG14.Signal=I2C1_SCL
PG2.GPIO_Label=BAT_INDICATOR4
PG2.Signal=GPIO_Output
PG3.GPIO_Label=BAT_INDICATOR5
PG3.Signal=GPIO_Output
PG4.GPIO_Label=LED_FATAL_ERROR
PG4.Signal=GPIO_Output
PG5.GPIO_Label=LED_POWER_ON
PG5.Signal=GPIO_Output
PG6.GPIO_Label=SW_FUNC
PG6.Signal=GPIO_Input
PG7.GPIO_Label=SW_CLR_ERR
PG7.Signal=GPIO_Input
PG8.GPIO_Label=SW_BAT_INDICATOR
PG8.Signal=GPIO_Input

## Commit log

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2024-07-09 Finished 5V_converter schematic, created .gitignore file, started drawing Servo_DC_converter schematic
    [5V_converter.SchDoc, Elkapod_power_supply.SchDoc, Servo_DC_converter.SchDoc]
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2024-07-17 Created Servos_controller schematic. Finished (maybe) the first version of the Logic_controller
    [Electronics_power_supply_DC_converter.SchDoc, Elkapod_power_supply.PrjPcb, Elkapod_power_supply.SchDoc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]
2024-07-18 Changed converters' switching frequency from 1MHz to 500kHz (standby coverter still working at 1MHz). Refactored schematics
    [Current_measurement_circuit.SchDoc, Electronics_power_supply_DC_converter.SchDoc, Elkapod_power_supply.PrjPcb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]
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2024-07-22 Fixing bus in progress
    [Controllable_voltage_outputs.SchDoc, Current_measurement_circuit.SchDoc, Electronics_power_supply_DC_converter.SchDoc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]
2024-07-23 Changed schematics, completed TODOs list, stated drawing PCB
    [Controllable_voltage_outputs.SchDoc, Current_measurement_circuit.SchDoc, Electronics_power_supply_DC_converter.SchDoc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]
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2024-07-24 Stated big refactoring. Started to split the project into two smaller PCBs
    [Controllable_voltage_outputs.SchDoc, Current_measurement_circuit.SchDoc, Electronics_power_supply_DC_converter.SchDoc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]
2024-07-25 Splited project to two separate modules: converter module and controller module
    [Controllable_voltage_outputs.SchDoc, Current_measurement.SchDoc, Current_measurement_circuit.SchDoc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]
2024-07-25 Corrected bugs causing errors. Numered scheets
    [Controllable_voltage_outputs.SchDoc, Current_measurement.SchDoc, Current_measurement_circuit.SchDoc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]
2024-07-30 Changed the approach from using peripheral ADC and GPIO axpanders to using bigger microcontroller. Drawing schematics in progress
    [Controllable_voltage_outputs.SchDoc, Elkapod_power_supply_controller_module.SchDoc, Logic_controller.SchDoc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]
2024-07-31 Refactored schematics of the Elkapod_power_supply_controller_module. Final version of the schematic using STM32L476ZETx
    [Controllable_voltage_outputs.SchDoc, Current_measurement_circuit.SchDoc, Elkapod_power_supply_controller_module.PrjPcb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]
2024-07-31 Added analog MUX for 4 temperature sensors. Started creating converters' PCB
    [Controllable_voltage_outputs.SchDoc, Current_measurement_circuit.SchDoc, Electronics_power_supply_DC_converter.SchDoc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]
2024-07-31 Changed pulling resistors on the power converters. Started placing components
    [Servos_DC_converter.SchDoc]
2024-08-01 Components placement in progress. Approach with LDOs on the PCB edge and goldpin socket in the centre.
    [Electronics_power_supply_DC_converter.SchDoc, StandBy_converter.SchDoc]
2024-08-06 Placing components in progress. Commit before change PCB shape form ractangle to U-shape
    [Electronics_power_supply_DC_converter.SchDoc, Elkapod_power_supply_converter_module.PrjPcb, Elkapod_power_supply_conveter_module.SchDoc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]
2024-08-06 Changed PCB shape to 'U'. Placing components in progress
    [Electronics_power_supply_DC_converter.SchDoc, Elkapod_power_supply_conveter_module.SchDoc, Servos_DC_converter.SchDoc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]
2024-08-07 Started creating the top PCB. Placed current measurement circuits for all servos. Started changing the top PCB shape to 'L'
    [Controllable_voltage_outputs.SchDoc, Current_measurement_circuit.SchDoc, Electronics_power_supply_DC_converter.SchDoc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]
2024-08-08 Pre-arrangement od components comleted on the both PCBs
    [Controllable_voltage_outputs.SchDoc, Current_measurement_circuit.SchDoc, Elkapod_power_supply_controller_module.SchDoc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]
2024-08-12 Changed 8-chanels ADC for 8 1-chanel ADCs on the converter board. Approach with GPIO expanders supply by 3,3VC voltage and ADCs supply by 5VC_DELAYED voltage
    [Electronics_power_supply_DC_converter.SchDoc, Elkapod_power_supply_converter_module.PrjPcb, Elkapod_power_supply_conveter_module.SchDoc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]
2024-08-13 Reducing PCB size in progress. Upper arm of PCB reduced by 15mm.
    [Current_measurement_circuit.SchDoc, Electronics_power_supply_DC_converter.SchDoc, Elkapod_power_supply_controller_module.SchDoc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]
2024-08-13 Reducing the power supply size in progress. Initially finished placing components on the bottom board.
    [Elkapod_power_supply_conveter_module.SchDoc]
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2024-08-15 Finished replacing components on the both PCBs due to reducing boards size
    [Elkapod_power_supply_controller_module.SchDoc, Logic_controller.SchDoc]
2024-08-19 3rd attempt to reduce the PCBs size completed, current dimensions of the bottom PCB 215x260mm
    [Elkapod_power_supply_conveter_module.SchDoc, Power_sources_selector.SchDoc]
2024-08-20 Changed packages of the AON7318 transistors. Tracing the converter PCB in progress.
    [Electronics_power_supply_DC_converter.SchDoc, Servos_DC_converter.SchDoc]
2024-08-21 Tracing the converters' PCB in progress. Commit before replacing stand-by converter components
    [Electronics_power_supply_DC_converter.SchDoc, Elkapod_power_supply_converter_module.PrjPcb, Servos_DC_converter.SchDoc]
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2024-08-23 Finished tracking upper arm of the bottom PCB
    [Elkapod_power_supply_conveter_module.SchDoc]
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2024-09-12 #2 Fixed problem with voltage levels in the servos enabling MOSFETs switchs. Started tracing the STM
    [Controllable_voltage_outputs.SchDoc, Current_measurement_circuit.SchDoc, Elkapod_power_supply_controller_module.SchDoc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]
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2024-09-24 #2 Fixing potential problems in the PCBs in progress. Replacement some components on the lower PCB
    [Current_measurement_circuit.SchDoc, Electronics_power_supply_DC_converter.SchDoc, Elkapod_power_supply_conveter_module.SchDoc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]
2024-09-27 Completed PCB change after potential issues were found. Thoroughly and finally checked top PCB. DRC performed on the top PCB
    [Controllable_voltage_outputs.SchDoc, Current_measurement_circuit.SchDoc, Elkapod_power_supply_controller_module.SchDoc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]
2024-10-13 Changed the bottom PCB after finding few potential problems in schematics. Added decoupling capacitors to few nets next to LM25116
    [Current_measurement_circuit.SchDoc, Electronics_power_supply_DC_converter.SchDoc, Elkapod_power_supply_controller_module.SchDoc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]
2024-10-13 #2 Finished changing PCBs after the final schematics check. Modified voltage feedbacks connections, increased mounting holes clearances. Did DRC
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2024-10-14 Checking the bottom PCB in progress. Found mistake with the temperature sensors
    [Elkapod_power_supply_conveter_module.SchDoc]
2024-10-16 #2 Finished checking the bottom PCB. Started modifing the upper PCB to add buzzer
    [Controllable_voltage_outputs.SchDoc, Current_measurement_circuit.SchDoc, Elkapod_power_supply_controller_module.SchDoc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]
2024-10-18 Updated schematics PDFs and STEP files, created GERBER files, added README file
    [Elkapod_power_supply_controller_module.PrjPcb, Elkapod_power_supply_converter_module.PrjPcb]
